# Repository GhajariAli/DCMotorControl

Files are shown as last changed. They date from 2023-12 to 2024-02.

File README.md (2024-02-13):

# DCMotorControl
I'll try to capture my Journey in getting a better understanding of a Motor Control, what's a best start other than a simple DC motor.

<details>
  
<summary>Parts I've used</summary>

- Swiss Maxon A-max 391116 Mini 22mm Coreless Motor DC 12V 24V 11000RPM High Speed (spoiler alert: it's max 2250rpm) [buy here](https://www.ebay.com/itm/263685368624)
  
 
- Rotary Encoder [buy here](https://www.aliexpress.com/item/4000094589182.html?spm=a2g0o.order_list.order_list_main.41.47f21802N3jsbi)


- Power Op-Amp [OPA548T](https://www.digikey.ca/en/products/detail/texas-instruments/OPA548T/266166)
- logic level Op-Amp for level shifting, Sallen-Key Filter, ... [LM324](https://www.digikey.ca/en/products/detail/texas-instruments/LM324N/277627)
- Nucleo STM32-F411RE dev board [buy here](https://www.digikey.ca/en/products/detail/stmicroelectronics/NUCLEO-F411RE/4866485)
- Resistors, Diodes, capacitors...

</details>

<details>

<summary>Tools I've used</summary>

- RIGOL DHO804 oscilloscope
- Two 30V-10A DC power Supply ( you need two to get + and - voltage since I don't use bridge setup at first)
- Bambu Lab P1S 3D printer
- of course a computer to program (Duh!)
- A Taranis X7 Controller and its receiver to send commands ( you don't need this necessarily but it's fun!)
- Also I used this Awsome plotter software [get it here](https://github.com/mich-w/QtSerialMonitor)

</details>

<details>

<summary>First Setup - Forward Direction Only</summary>

Just to make things more fun I've started with the encoder mentioned above and made this setup: 



later on moved to this to have it more stable:



All models can be find in the 3D model folder

Basic circuit for this setup (you can find it in the KiCAD folder):


This can do forward direction only for speed control with relative encoder.
List of Branches:
- [This branch](https://github.com/GhajariAli/DCMotorControl/tree/VelocityControl_GPIO_Encoder) is to read the encoder with normal GPIO 
- [This branch](https://github.com/GhajariAli/DCMotorControl/tree/InterruptEncoder_VelocityControl) is to read the encoder with Interrupt 
- [This branch](https://github.com/GhajariAli/DCMotorControl/tree/VelocityControl_TimerEncoderMode) is to read the encoder with Timer in Encoder Mode ( this is easiest and probably best way, the other two was just to practive and for fun of it) 

</details>

<details>

<summary>Second Setup - Bidirectional Control</summary>

in order to have both position and velocity control I moved to an absolute encodr and I made it myself!
[This branch](https://github.com/GhajariAli/DCMotorControl/tree/BidirectionSpeedandPosition) is the final branch with the new circuit that can control the motor direction and speed with the same power op-amp



Here is the absolute encoder disc I made :



it's an 8 bit ablsute encoder which is using gray code to have less error on reading the position.

I've used some cheap IR transmitter and receiver diodes and made some sort of a stand for it as below 




The IR sensors can be purcahsed [here](https://www.aliexpress.com/item/1005005371811048.html?spm=a2g0o.order_list.order_list_main.21.61131802yJksCa)

and you can easily drive them with 1k resistor on transmitter and 10k on receiver ( no amplification or comparator needed for 3.3V logic level )



and of course you'll find all my 3d designs in the 3d model folder



Position Control Results


Velocity Control Results


mechanical parts not being perfect and low resolution of the encoder causes sthe fluctuations you see, otherwise it's controlling pretty good.

Watch Here:

Watch the video (https://www.youtube.com/shorts/_Hv775r4zMI)
Watch the video (https://www.youtube.com/shorts/p1Zbr400qCg)

</details>

<details>

<summary>Improvements - Speed control by Voltage reading</summary>

[This](https://github.com/GhajariAli/DCMotorControl.git) is the branch for this feature. some improvement and correction in the main circuit that will be merged into the [main](https://github.com/GhajariAli/DCMotorControl.git) 

Here is the new circuit - you'll find it in the KiCAD folder MotorControl-V2



Here is How it looks on the scope, I'm disabling the power op-amp for around 300 usec and read the voltage after some level shifting and clipping in channel 1 of the ADC. 
the big pulse is the op-amp enable pulse and the blue line is the motor voltage to condition and read by ADC:



here is the speed reading results, red is the encoder feedback and blue is the voltage reading, notice it's clipped as I decided to not scale it down with voltage divider since it already had lots of fluctuation and noise. also some delay due the wait time in the mcu ( to let the self induce voltage caused by cutting motor current to dampen) 



as nice at it looks, I decided not to use this as a control feedback as the encoder works mych better:) but it's fun doing it.

</details>

Stay Tuned, AC Induction Motor is next!

Update: [Here](https://github.com/GhajariAli/InductionMotorControl) is the Induction Motor Repo

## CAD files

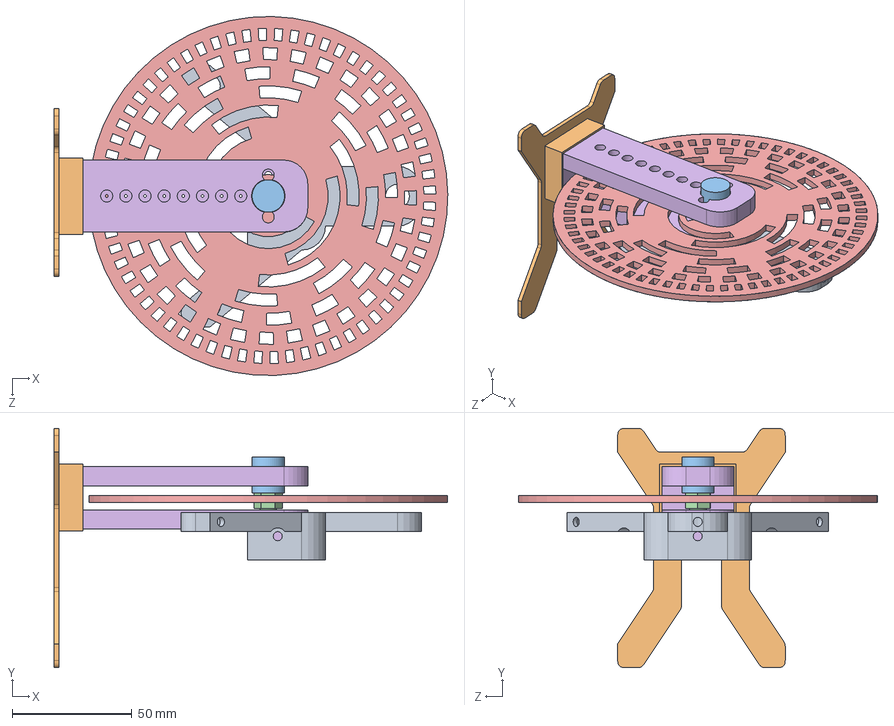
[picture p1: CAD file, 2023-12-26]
3DModels/Absolute encoder/EncoderAsyV3.SLDASM
164.4 x 100.0 x 150.0 mm
IRTest2
encoderV3
EncoderV3ShaftP1
EncoderV3ShaftP2
V3Stand
V3Stablizer

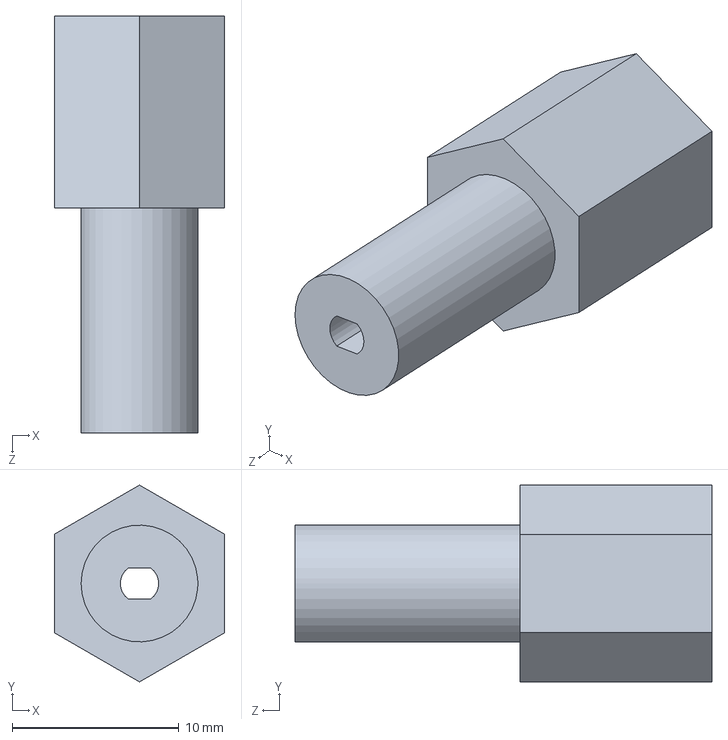
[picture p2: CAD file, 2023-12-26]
3DModels/Absolute encoder/EncoderV3ShaftP1.SLDPRT
10.2 x 11.8 x 25.0 mm

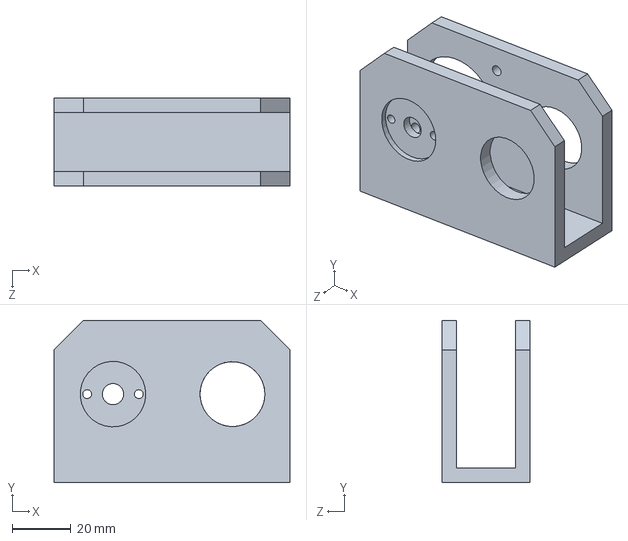
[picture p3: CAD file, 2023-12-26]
3DModels/Relative encoder/baseV2.SLDPRT
80.0 x 55.0 x 30.0 mm

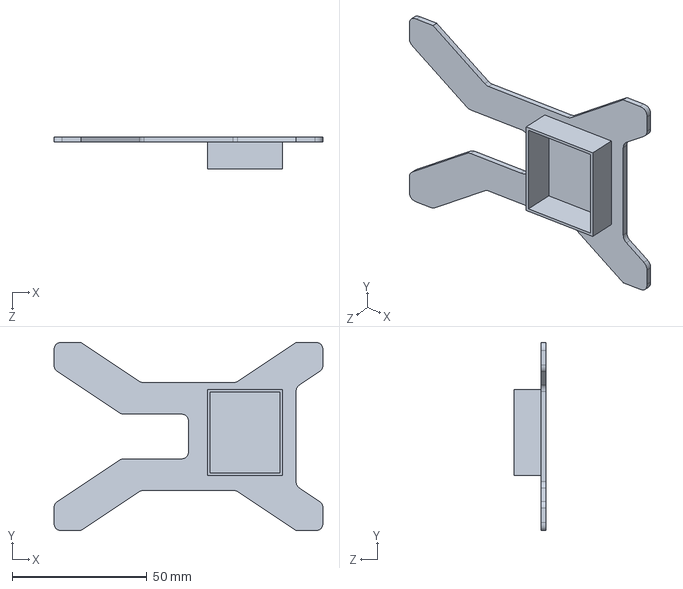
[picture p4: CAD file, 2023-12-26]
3DModels/Absolute encoder/V3Stand.SLDPRT
100.0 x 70.0 x 12.0 mm

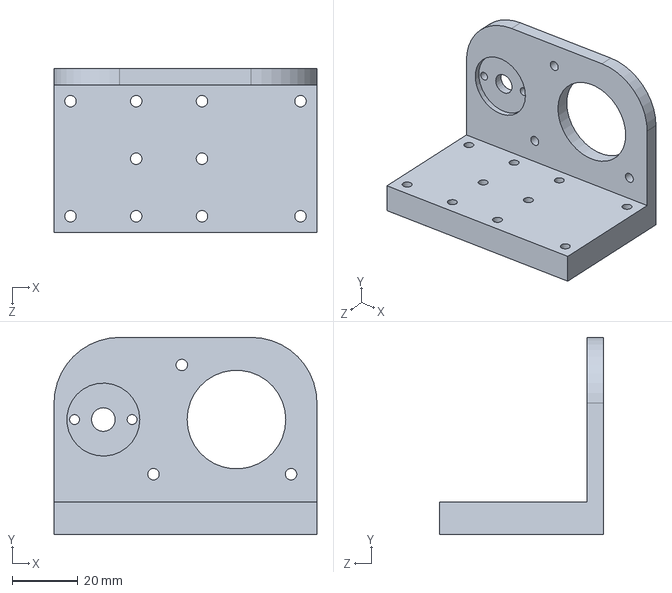
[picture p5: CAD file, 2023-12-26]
3DModels/Relative encoder/base.SLDPRT
80.0 x 60.0 x 50.0 mm

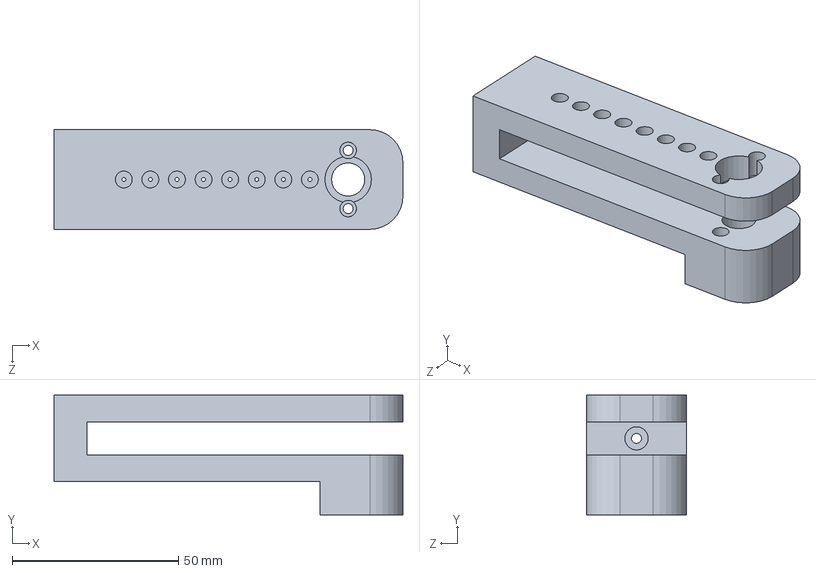
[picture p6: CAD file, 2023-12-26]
3DModels/Absolute encoder/IRTest2.SLDPRT
105.0 x 36.0 x 30.0 mm

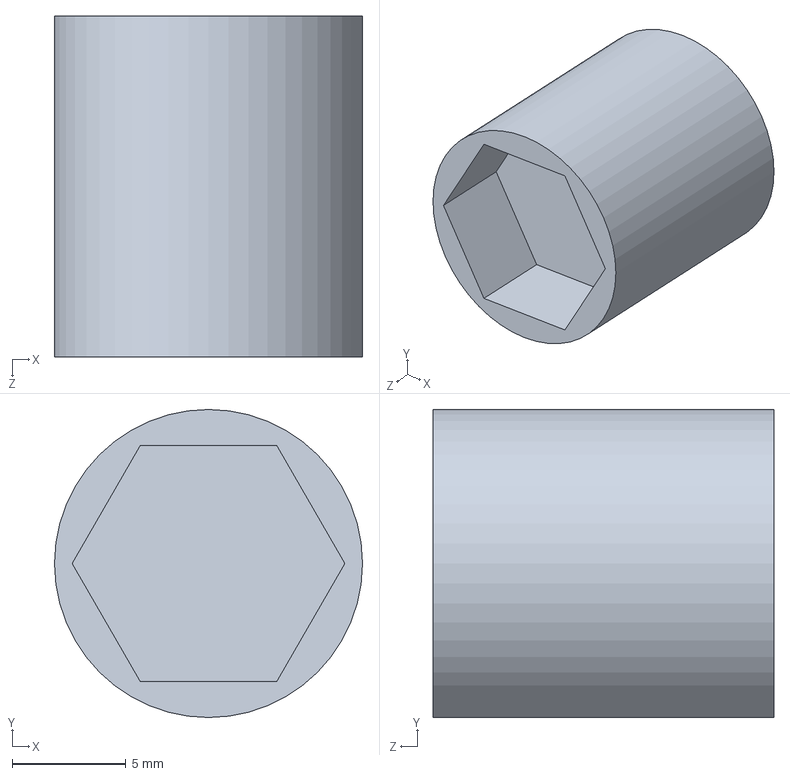
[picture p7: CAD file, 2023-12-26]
3DModels/Absolute encoder/EncoderV3ShaftP2.SLDPRT
13.6 x 13.6 x 15.0 mm

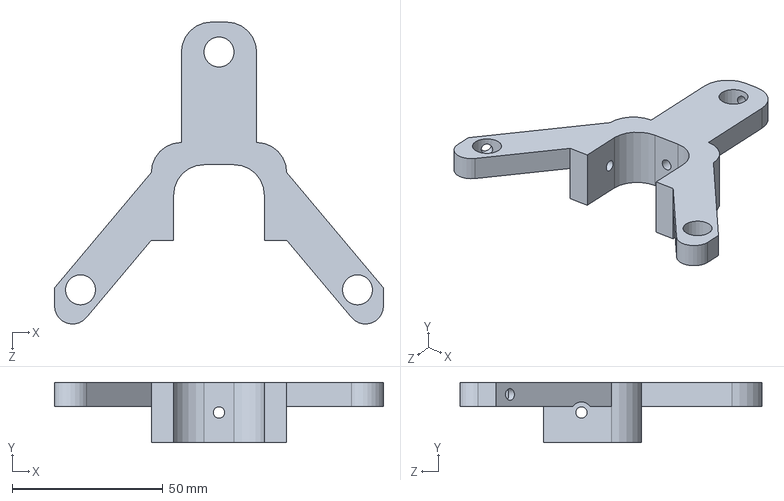
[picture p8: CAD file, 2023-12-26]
3DModels/Absolute encoder/V3Stablizer.SLDPRT
109.3 x 20.0 x 100.3 mm

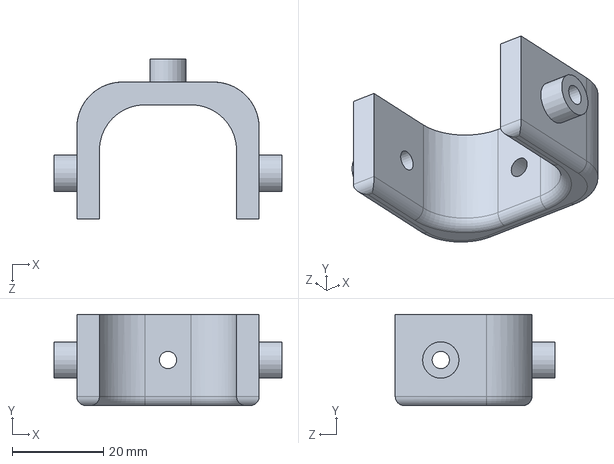
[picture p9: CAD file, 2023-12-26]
3DModels/Absolute encoder/V3StablizerP2.SLDPRT
50.0 x 20.0 x 35.0 mm

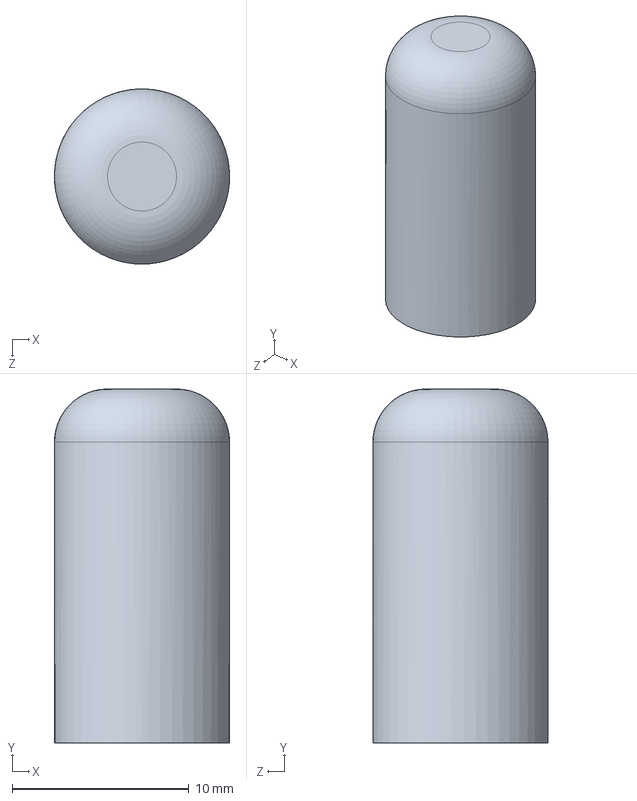
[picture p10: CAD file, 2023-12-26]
3DModels/Absolute encoder/V3StablizerPin.SLDPRT
9.90 x 20.0 x 9.90 mm

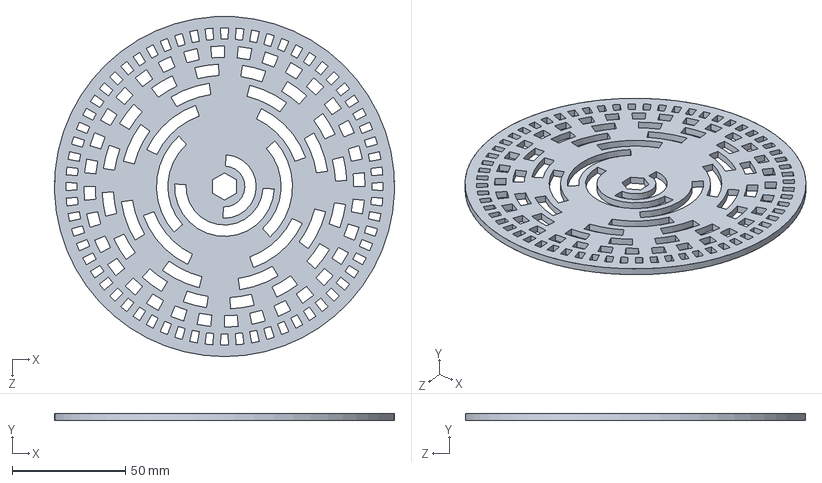
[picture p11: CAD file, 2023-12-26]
3DModels/Absolute encoder/encoderV3.SLDPRT
149.9 x 3.00 x 150.0 mm

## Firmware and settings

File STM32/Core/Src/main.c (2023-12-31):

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
/* Includes ------------------------------------------------------------------*/
#include "main.h"

/* USER CODE BEGIN Includes */
#include <stdio.h>
#include "Sbus.h"
#include "encoder.h"
#include "PID.h"
/* USER CODE END Includes */

/* USER CODE BEGIN PTD */
tsbus receivedSBUS;
uint32_t SystemTime = 0;
encoder_data TestEncoder;
PID_Controller PID;
int speedChangerPulse=0;
int messageUpdateTime=0;
int speedUpdateTime=0;
int uart2Free=1;
int OperationMode=0;
int PreviousOperationMode=0;
uint32_t Timer2Counter=0;
int ADCReadingInProgress=0;
uint32_t MotorVoltageRaw=0;
int32_t ProcessValue=0;
int ModuloSetpoint;
int ModuloFeedback;
/* USER CODE END PTD */

ADC_HandleTypeDef hadc1;

TIM_HandleTypeDef htim1;
TIM_HandleTypeDef htim2;

UART_HandleTypeDef huart1;
UART_HandleTypeDef huart2;
DMA_HandleTypeDef hdma_usart1_rx;

/* USER CODE BEGIN PV */
void HAL_UART_RxCpltCallback(UART_HandleTypeDef *huart){
	if (huart == &huart1){
		ParseSBUS(&receivedSBUS);
	}
}
void HAL_UART_TxCpltCallback(UART_HandleTypeDef *huart){
	if (huart == &huart2){
		uart2Free=1;
	}
}
#ifdef ENCODER_INTERRUPT_MODE
void HAL_GPIO_EXTI_Callback(uint16_t GPIO_Pin)
{
  if(GPIO_Pin==Encoder_A_Pin){TestEncoder.IT_EncoderChA= HAL_GPIO_ReadPin(Encoder_A_GPIO_Port, Encoder_A_Pin);}
  else if (GPIO_Pin==Encoder_B_Pin){TestEncoder.IT_EncoderChB= HAL_GPIO_ReadPin(Encoder_B_GPIO_Port, Encoder_B_Pin);}
}
#endif
#ifdef ENCODER_TIMER_MODE
void HAL_TIM_IC_CaptureCallback(TIM_HandleTypeDef *htim){
	if (htim == &htim2){
		TestEncoder.EncoderValue = __HAL_TIM_GET_COUNTER(htim);
	}
}
#endif
/* USER CODE END PV */

void SystemClock_Config(void);
static void MX_GPIO_Init(void);
static void MX_DMA_Init(void);
static void MX_USART2_UART_Init(void);
static void MX_TIM1_Init(void);
static void MX_USART1_UART_Init(void);
static void MX_ADC1_Init(void);
static void MX_TIM2_Init(void);
/**
  * @brief  The application entry point.
  * @retval int
  */
int main(void)
{
  /* MCU Configuration--------------------------------------------------------*/

  /* Reset of all peripherals, Initializes the Flash interface and the Systick. */
  HAL_Init();

  /* Configure the system clock */
  SystemClock_Config();

  /* Initialize all configured peripherals */
  MX_GPIO_Init();
  MX_DMA_Init();
  MX_USART2_UART_Init();
  MX_TIM1_Init();
  MX_USART1_UART_Init();
  MX_ADC1_Init();
  MX_TIM2_Init();
  /* USER CODE BEGIN 2 */
  HAL_UART_Receive_DMA(&huart1, &receivedSBUS.ReceivedData[0], SBUS_LEN);
  HAL_TIM_Base_Start_IT(&htim1);
  HAL_TIM_Base_Start(&htim2);
  HAL_ADC_Start(&hadc1);
  HAL_TIM_PWM_Start(&htim1, TIM_CHANNEL_1);
  SystemTime=HAL_GetTick();
  TestEncoder.PreviusGrayCode=0;
  TestEncoder.EncoderValue=0;
  TestEncoder.PreviousEncoderValue=0;
  TestEncoder.SpeedRPM=0;
  TestEncoder.direction=CW;
  PID.Kp=5;
  PID.Ki=0.6;
  PID.Kd=0.1;
  PID.dt=10;
  PID.integral=0;
  PID.min_output= 0;
  PID.max_output= 1000;
  PID.min_Integral= -500;
  PID.max_Integral= 500;
  PID.output=5000;
  PID.target=0;
  HAL_GPIO_WritePin(Motor_Enable_GPIO_Port, Motor_Enable_Pin, GPIO_PIN_SET);
  /* USER CODE END 2 */

  /* Infinite loop */
  /* USER CODE BEGIN WHILE */

  while (1)
  {

	  //read Encoder
	  GetEncoderValue(&TestEncoder);
	  //reading SBUS from remote controller and writing PWM output
	  if (!HAL_GPIO_ReadPin(B1_GPIO_Port, B1_Pin)){
		  while(!HAL_GPIO_ReadPin(B1_GPIO_Port, B1_Pin)){}
		  if (OperationMode==3){
			  OperationMode=0;
		  }
		  else OperationMode++;
	  }
	  switch (OperationMode) {
	  case 0://get speed command from remote controller
		  PID.Kp=1.2;
		  PID.Ki=0.8;
		  PID.Kd=0;
		  PID.target = 0 ;
		  ProcessValue= TestEncoder.SpeedRPM;
		  PID.ControlMode=Velocity;
		  PreviousOperationMode=OperationMode;
		  break;
	  case 1: //Position control
		  if (PreviousOperationMode!=OperationMode){
			  PID.Kp=0.75;
			  PID.Ki=0.08;
			  PID.Kd=0.16;
			  PID.output=0;
			  PID.target=0;
			  PID.integral=0;
		  }

		  if (receivedSBUS.ch[2]>200 && receivedSBUS.ch[2]<1800){
			  ModuloSetpoint = (receivedSBUS.ch[2]-200)*360/1600;
		  }
		  else if(receivedSBUS.ch[2]<200){
			  ModuloSetpoint=0;
		  }
		  else if(receivedSBUS.ch[2]>1800){
			  ModuloSetpoint=360;
		  }
		  PID.target = ModuloSetpoint *256/360;
		  PID.ControlMode=Position;
		  ProcessValue= TestEncoder.GrayCode;
		  ModuloFeedback= ProcessValue*360/256;
		  PreviousOperationMode=OperationMode;
		  break;
	  case 2:
		  PID.Kp=1.2;
		  PID.Ki=0.8;
		  PID.Kd=0;
		  PID.ControlMode=Velocity;
		  if (receivedSBUS.ch[1]>1000 && receivedSBUS.ch[1]<2000){
			  PID.target = 2* ( receivedSBUS.ch[1]-1000);
		  }
		  else if (receivedSBUS.ch[1]>0 && receivedSBUS.ch[1]<990){
			  PID.target = -2* (990- receivedSBUS.ch[1]);
		  }
		  else{
			  PID.target=0;
		  }
		  ProcessValue= TestEncoder.SpeedRPM;
		  PreviousOperationMode=OperationMode;
		  break;
	  case 3: // toggle speed automatically
		  if (PreviousOperationMode!=OperationMode){
			  PID.Kp=1.2;
			  PID.Ki=0.8;
			  PID.Kd=0;
			  PID.target=250;
		  }
		  PID.ControlMode=Velocity;
		  if(HAL_GetTick()-speedUpdateTime>=10000){
	 		  if(PID.target==-250) PID.target=250;
	 		  else if (PID.target==250) PID.target=-250;
	 		  speedUpdateTime=HAL_GetTick();

		  }
		  ProcessValue= TestEncoder.SpeedRPM;
		  PreviousOperationMode=OperationMode;
		  break;

	  }

	  //Calculate RPM
	  //with motor Voltage

	  Timer2Counter=__HAL_TIM_GET_COUNTER(&htim2);
	  if (Timer2Counter>=1000000 || ADCReadingInProgress){//every 100 @ 100MHZ will be 1 micro-second so 1000000 will be 10ms
		  if (ADCReadingInProgress==0){
			  __HAL_TIM_SET_COUNTER(&htim2,0);
		  }
		  ADCReadingInProgress= __HAL_TIM_GET_COUNTER(&htim2);
		  HAL_GPIO_WritePin(Motor_Enable_GPIO_Port, Motor_Enable_Pin, GPIO_PIN_RESET);
		  if (ADCReadingInProgress>=25000){//wait 250 usec before reading ADC
			  int ADCStatus=10;
			  ADCStatus=HAL_ADC_PollForConversion(&hadc1,1);
			  if(ADCStatus==0){
				  MotorVoltageRaw=HAL_ADC_GetValue(&hadc1);
				  HAL_ADC_Start(&hadc1);
				  __HAL_TIM_SET_COUNTER(&htim2,0);
				  HAL_GPIO_WritePin(Motor_Enable_GPIO_Port, Motor_Enable_Pin, GPIO_PIN_SET);
				  ADCReadingInProgress=0;
			  }
		  }


	  }
	  //with Encoder
	  if (HAL_GetTick()-SystemTime>=(PID.dt)){
		  TestEncoder.SpeedRPM=(TestEncoder.EncoderValue-TestEncoder.PreviousEncoderValue)*(1000/PID.dt)*60/256;//1000/dt for converting to pulse per second - 60 for 1sec to 1min - 256 for pules/rev - for gray code to pulse
		  TestEncoder.PreviousEncoderValue=TestEncoder.EncoderValue;
		  SystemTime=HAL_GetTick();
		  updatePID(&PID, ProcessValue);
		  __HAL_TIM_SET_COMPARE(&htim1,TIM_CHANNEL_1,PID.output);
	  }
	  if (HAL_GetTick()-messageUpdateTime>=50){
		  char message[100];
		  int messagaLen=0;
		  messagaLen=sprintf(&message,"Spd=%ld, SpdSet=%f,PosSet=%d, PosFB=%d, Volt=%d T=%d ,\n",ProcessValue,PID.target,ModuloSetpoint,ModuloFeedback,(MotorVoltageRaw*6/10)-1200,messageUpdateTime);
		  if (uart2Free==1){
			  HAL_UART_Transmit_IT(&huart2, message, messagaLen);
			  uart2Free=0;
		  }
		  messageUpdateTime=HAL_GetTick();
	  }

    /* USER CODE END WHILE */

    /* USER CODE BEGIN 3 */
  }
  /* USER CODE END 3 */
}

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


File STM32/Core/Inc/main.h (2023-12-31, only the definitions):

#define B1_Pin GPIO_PIN_13
#define B1_GPIO_Port GPIOC
#define Motor_Enable_Pin GPIO_PIN_1
#define Motor_Enable_GPIO_Port GPIOC
#define Motor_Voltage_Pin GPIO_PIN_1
#define Motor_Voltage_GPIO_Port GPIOA
#define USART_TX_Pin GPIO_PIN_2
#define USART_TX_GPIO_Port GPIOA
#define USART_RX_Pin GPIO_PIN_3
#define USART_RX_GPIO_Port GPIOA
#define Encoder_2_Pin GPIO_PIN_5
#define Encoder_2_GPIO_Port GPIOA
#define Encoder_3_Pin GPIO_PIN_6
#define Encoder_3_GPIO_Port GPIOA
#define Encoder_4_Pin GPIO_PIN_7
#define Encoder_4_GPIO_Port GPIOA
#define Encoder_6_Pin GPIO_PIN_7
#define Encoder_6_GPIO_Port GPIOC
#define TMS_Pin GPIO_PIN_13
#define TMS_GPIO_Port GPIOA
#define TCK_Pin GPIO_PIN_14
#define TCK_GPIO_Port GPIOA
#define SWO_Pin GPIO_PIN_3
#define SWO_GPIO_Port GPIOB
#define Encoder_7_Pin GPIO_PIN_4
#define Encoder_7_GPIO_Port GPIOB
#define Encoder_5_Pin GPIO_PIN_6
#define Encoder_5_GPIO_Port GPIOB
#define Encoder_0_Pin GPIO_PIN_8
#define Encoder_0_GPIO_Port GPIOB
#define Encoder_1_Pin GPIO_PIN_9
#define Encoder_1_GPIO_Port GPIOB

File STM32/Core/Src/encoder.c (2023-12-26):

#include "encoder.h"
#include "main.h"

void GetEncoderValue(encoder_data *encoder){
	  int EncoderGrayConvert[8] ={0,0,0,0,0,0,0,0};
	  int GrayCode=0;
	  int GrayMSBDetected = 0;
	  //reading encoder value as gray code
#ifdef ENCODER_GPIO_MODE
	  //EncoderGrayCode = GrayCodeConvert[(HAL_GPIO_ReadPin(Encoder_A_GPIO_Port, Encoder_A_Pin) <<1 | HAL_GPIO_ReadPin(Encoder_B_GPIO_Port, Encoder_B_Pin)) & 0x03];
	  int b[8];
	  b[0]=!HAL_GPIO_ReadPin(Encoder_0_GPIO_Port, Encoder_0_Pin);
	  b[1]=!HAL_GPIO_ReadPin(Encoder_1_GPIO_Port, Encoder_1_Pin);
	  b[2]=!HAL_GPIO_ReadPin(Encoder_2_GPIO_Port, Encoder_2_Pin);
	  b[3]=!HAL_GPIO_ReadPin(Encoder_3_GPIO_Port, Encoder_3_Pin);
	  b[4]=!HAL_GPIO_ReadPin(Encoder_4_GPIO_Port, Encoder_4_Pin);
	  b[5]=!HAL_GPIO_ReadPin(Encoder_5_GPIO_Port, Encoder_5_Pin);
	  b[6]=!HAL_GPIO_ReadPin(Encoder_6_GPIO_Port, Encoder_6_Pin);
	  b[7]=!HAL_GPIO_ReadPin(Encoder_7_GPIO_Port, Encoder_7_Pin);
	  encoder->EncoderRawValue =(b[7] <<7 | b[6] <<6 | b[5] <<5 | b[4] <<4 | b[3] <<3 | b[2] <<2 | b[1] <<1 | b[0]) & 0b11111111;
	  //To convert Gray to Binary write the most significant bit MSB then compare the next bit with that if similar put 0 if different put 1
	  for (int index = 7 ; index >= 0 ; index--){
	          if ((b[index]==1) & ! (GrayMSBDetected)) {
	        	  EncoderGrayConvert[index]=b[index];
	              GrayMSBDetected=index;
	          }
	          if(GrayMSBDetected){
	              if (EncoderGrayConvert[index+1]==b[index]) EncoderGrayConvert[index]=0;
	              else EncoderGrayConvert[index]=1;
	          }
	  }
	  encoder->GrayCode  = GrayCode =((   EncoderGrayConvert[7] <<7 |
										  EncoderGrayConvert[6] <<6 |
										  EncoderGrayConvert[5] <<5 |
										  EncoderGrayConvert[4] <<4 |
										  EncoderGrayConvert[3] <<3 |
										  EncoderGrayConvert[2] <<2 |
										  EncoderGrayConvert[1] <<1 |
										  EncoderGrayConvert[0]) & 0b11111111);
#endif
#ifdef ENCODER_INTERRUPT_MODE
	  EncoderGrayCode = GrayCodeConvert[(encoder->IT_EncoderChA <<1 | encoder->IT_EncoderChB) & 0x03];
#endif

#ifndef ENCODER_TIMER_MODE //the value will be written in main.c in timer interrupt function
	  //if encoder value updated
	  if (encoder->PreviusGrayCode != GrayCode){
		  int EncoderDeltaValue;
		  EncoderDeltaValue = GrayCode-encoder->PreviusGrayCode;
		  if (EncoderDeltaValue<0) {EncoderDeltaValue+=4;}
		  if (EncoderDeltaValue ==1) {
			  encoder->direction=CW;
			  encoder->EncoderValue++;
		  }
		  else if (EncoderDeltaValue ==3){
			  encoder->direction=CCW;
			  encoder->EncoderValue--;
		  }
		  encoder->PreviusGrayCode=GrayCode;
	 }
#else
	  if (encoder->EncoderValue >=0){ encoder->direction = CW;}
	  else {encoder->direction = CCW;}
#endif
}

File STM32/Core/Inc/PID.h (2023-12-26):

enum Mode{
	Velocity = 0,
	Position = 1,
	Torque = 2,
};

typedef struct{
	enum Mode ControlMode;
    double Kp;
    double Ki;
    double Kd;
    double min_output;
    double max_output;
    double min_Integral;
    double max_Integral;
    double target;
    double CurrentError;
    double prev_error;
    double integral;
    double dt; //sample time in msec
    double output;
}PID_Controller;
#define ENCODER_RESOLUTION 256
#define PWM_MAXVALUE	1000


void updatePID(PID_Controller* pid, double current);

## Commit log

2023-11-09 adds encoder reading
2023-11-17 reading speed with encoder
2023-11-19 adds PID logic wip
2023-11-19 tunes pid
2023-11-20 adds timestampt to the uart data to plotter app
2023-11-20 uses Cube labels for encoder
2023-11-20 adds input mode selection via push button - toggle between auto setpoint or radio control SBUS
2023-11-21 adds encoder reading via interrupt
2023-11-26 encoder reads in timer mode
2023-11-26 pid tuning - new setup
2023-12-26 adds velocity and position control modes
2023-12-26 adds KiCAD project
    [MotorControl.kicad_pcb, MotorControl.kicad_sch]
2023-12-26 adds 3D models
    [base.SLDPRT, baseV2.SLDPRT]
2023-12-26 adds basic circuit
    [MotorControl V1.kicad_sch, MotorControl.kicad_pcb, MotorControl.kicad_sch]
2023-12-26 adds absolute 3d model
    [EncoderAsyV3.SLDASM, EncoderV3ShaftP1.SLDPRT, EncoderV3ShaftP2.SLDPRT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]
2023-12-26 remove extras
    [MotorControl.kicad_pcb, MotorControl.kicad_sch]
2023-12-27 adds enable circuit
    [MotorControl.kicad_sch]
2023-12-29 improving circuit
    [MotorControl.kicad_sch]
2023-12-29 update circuits
    [MotorControl.kicad_sch]
2023-12-29 adds motor voltage reading

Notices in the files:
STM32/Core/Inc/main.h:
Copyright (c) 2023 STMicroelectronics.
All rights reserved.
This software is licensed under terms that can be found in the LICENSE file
